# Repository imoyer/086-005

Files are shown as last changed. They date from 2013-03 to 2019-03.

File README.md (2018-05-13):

# 086-005

Gestalt Single Stepper Node Firmware

## Introduction

This is the firware the Single Node board used in the Gestalt project by Ilan and Nadya. Which is nice. In this repository you will find files needed to program your Gestalt Single Stepper Node. You can find the files for PCB production in the [board](board) folder of this repository. Pick your revision (e.g. `rev0.4`) and make your own board!

## Installation

This repository contains [Makefile](Makefile) which is used by `make` to do the following.

1. Burn the firmware
2. Set the fuses

At the moment it is configured to use the **AVRISP mkII**. To make it work with FabISP or other AVR programmer, a lot of people will be happy if you add your custom code and make a pull request.

**First** make sure that your AVR programmer is connected. There are many ways to do it, I used `lsusb` on a MacOS system.

```
lsusb
```

The following is what I got in the list.

```
Atmel Corporation AVRISP mkII
```

Which is exactly what I need to proceed. We assume that things like `avrdude` or [CrossPack](https://www.obdev.at/products/crosspack/index.html) are already installed.

**Second**, make sure your Gestalt Node is properly connected to a power source, FTDI and AVR programmer.

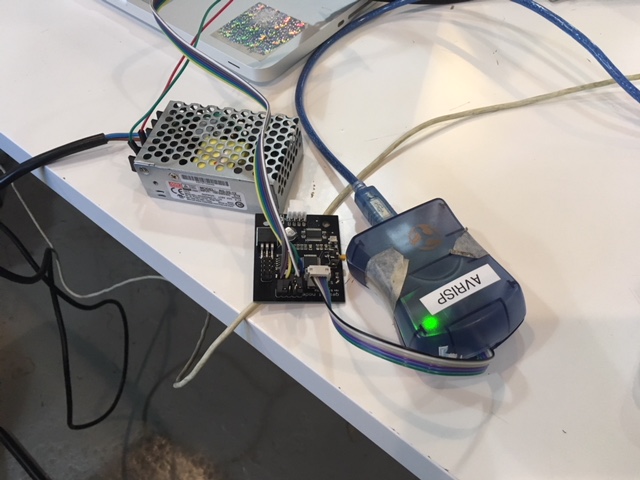
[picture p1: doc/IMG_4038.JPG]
Connected to AVR programmer


At this point you can use `make` to burn the firmware.

```
make program-avrisp2
```

You should see output with things that look like progress bars and a polite **Thank you!** at the end. 

**Third** make sure that you set the fuses. For that you have to use `make` once more.

```
make program-avrisp2-fuses
```

It might ask you to reset a fuse on the way, **just hit ENTER** unless you know what you are doing.

**Congratulations!** Your Gestalt Node is ready to be used. Now go to the [pygestalt](https://github.com/nadya/pygestalt) repository and continue from there.

## Contributing

Please add anything weird to the issue tracker of this repository. If you see how you can improve things directly, submit a pull request.

Thank you!

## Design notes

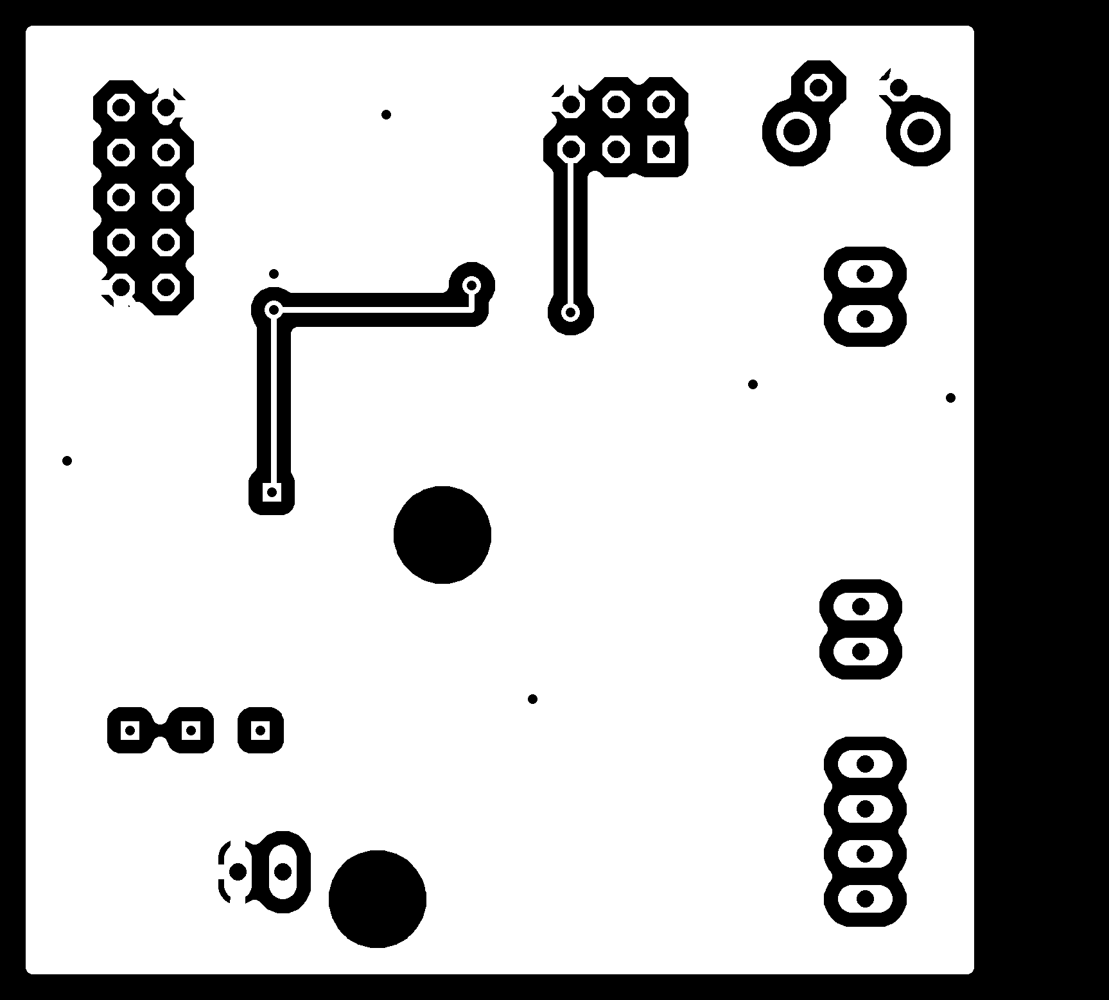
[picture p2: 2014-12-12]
board/extruder/extruder-bottom.png

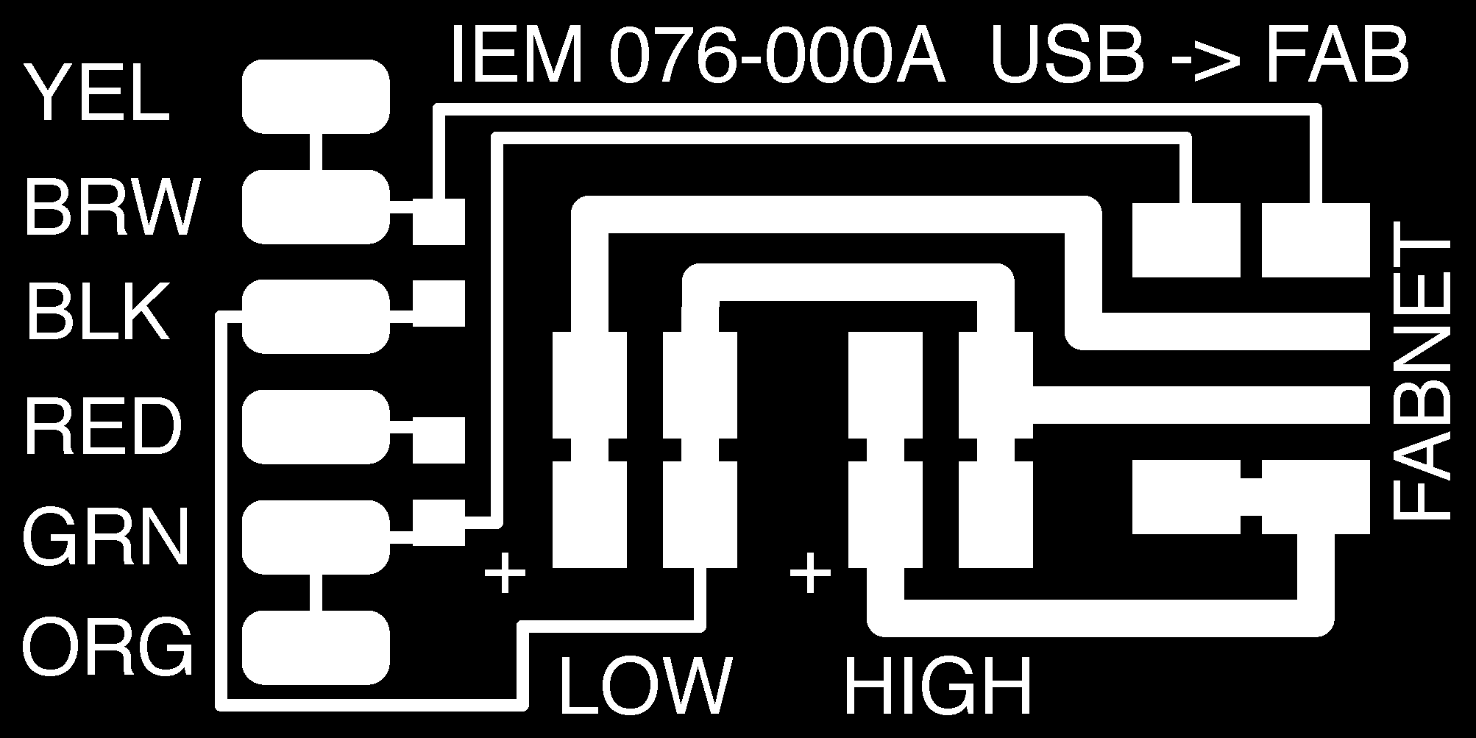
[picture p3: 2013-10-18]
board/fabnet_adapter/076-000Ar1.png

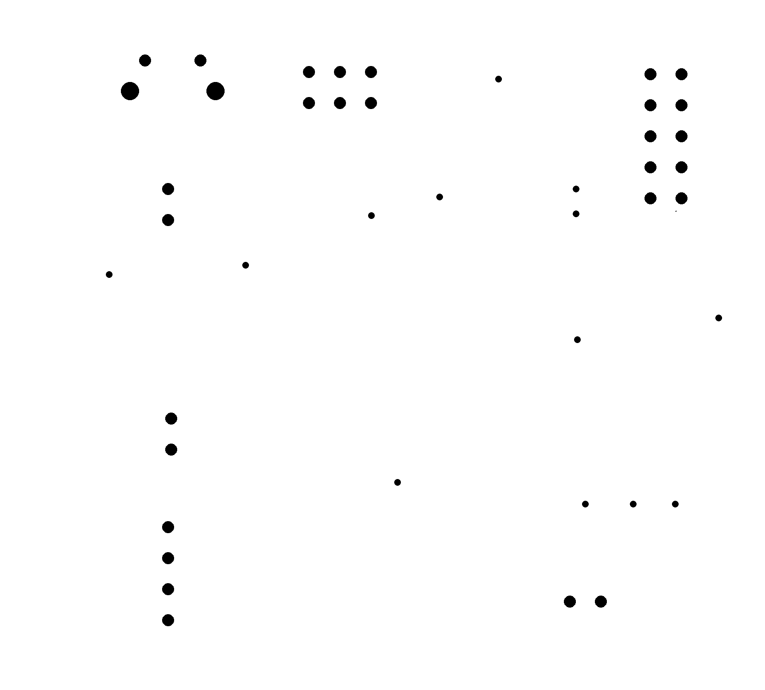
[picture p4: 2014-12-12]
board/extruder/extruder-holes.png

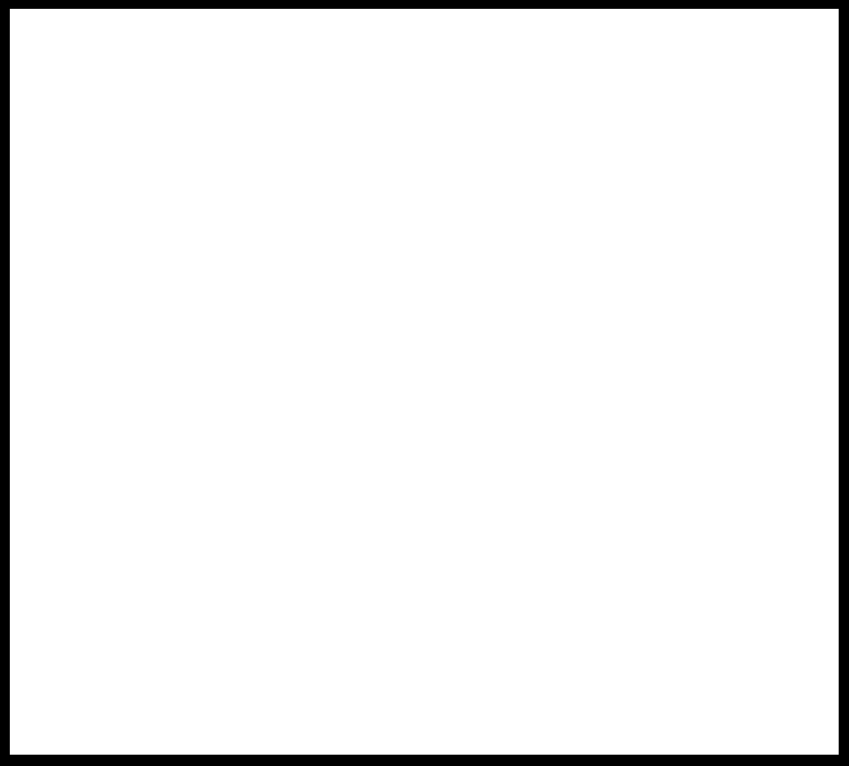
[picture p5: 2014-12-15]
board/extruder/extruder-outline.png

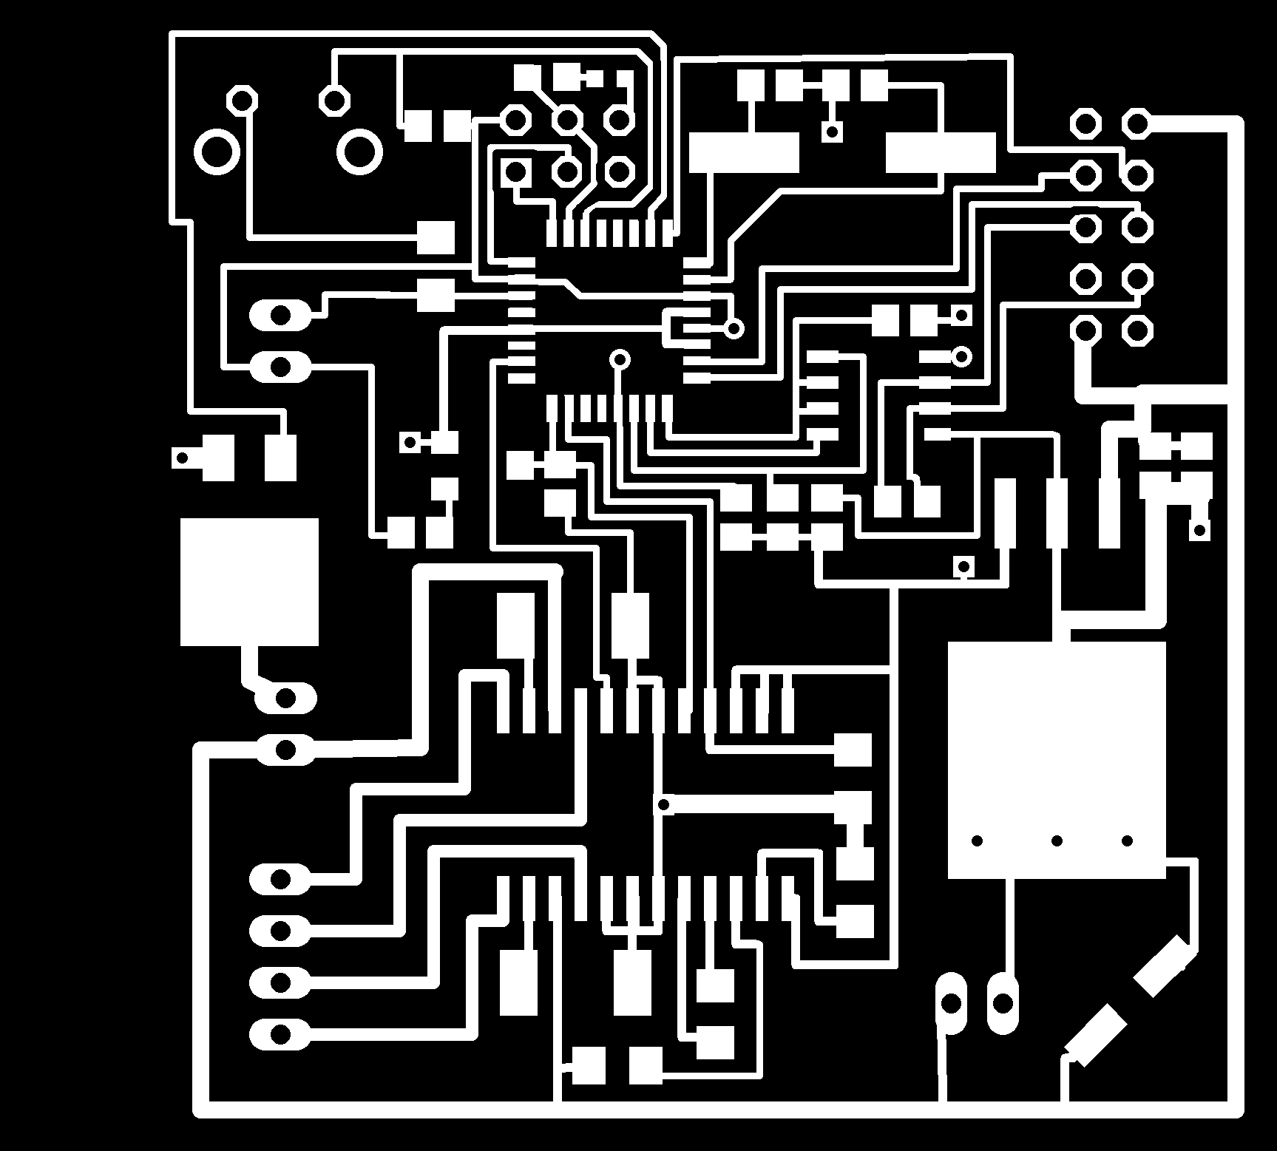
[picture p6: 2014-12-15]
board/extruder/extruder-traces.png

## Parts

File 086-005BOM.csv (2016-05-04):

Name | Description | package | Manufacturer | part | nr | Vendor | part | nr | quantity | unit | price | extended | price
gestalt | network | BOM
usb | to | serial | cable | CABLE | USB | RS485 | WIRE | END | 1.8M |  | USB-RS485-WE-1800-BT | 768-1041-ND | 1 | 30 | 30
fabbus | plugs | 10pin | idc | connector | 0.1 | in
fabbus | ribbon | cabling | 22 | gauge | 10 | wire | ribbon
fabbus | resistors | 540 | ohms?
gestalt | node | BOM
motor | jack | molex | kk | kk | 22-05-3041 | WM4302-ND | 1 | 0.71 | 0.71
motor | plug | molex | kk | with | wings | kk | 22013047 | WM2002-ND | 1 | 0.2 | 0.2 | note | don't | need | this | for | node
motor | crimps | molex | kk | kk | 8500114 | WM1114-ND | 4 | 0.18 | 0.72 | note | don't | need | this | for | node
microcontroller | IC | MCU | 8BIT | 32KB | FLASH | 32TQFP | tqfp | atmega328p | ATMEGA328P-ANRCT-ND | 1 | 4.03 | 4.03
stepper | motor | driver | IC | MOTOR | DRIVER | PAR | 24TSSOP | 24tssop | A4982SLPTR-T | 620-1352-1-ND | 1 | 3.66 | 3.66
differential | bus | transceiver | IC | DIFF | BUS | TRANSCEIVER | 8-SOIC | 8-soic | SN75176AD | 296-6857-5-ND | 1 | 0.96 | 0.96
5v | regulator | IC | REG | LDO | 5V | 1.5A | DDPAK | d2pak-3 | TL780-05CKTTR | 296-20777-1-ND | 1 | 0.95 | 0.95
button | SWITCH | TACTILE | SPST-NO | 0.05A | 24V | Through Hole, Right Angle | B3F-3152 | SW410-ND | 1 | 0.54 | 0.54
potentiometer | TRIMMER | 5K | OHM | 0.25W | SMD | top adjustment, Gull Wing | PVG3G502C01R00 | 490-6996-1-ND | 1 | 1.04 | 1.04
40mm | x | 40mm | fan | FAN | 40X10MM | 12VDC | 0.96W | 7CFM |  | MB40101V2-000U-A99 | 259-1564-ND | 1 | 1 | 4.53 | note, don't need this
fan | connector |  |  |  |  |  |  | 0 | note, don't need this
18.432MHz | crystal | CRYSTAL | 18.432MHZ | 18PF | SMD | hc49/us | ECS-184-18-5PX-TR | XC1285CT-ND | 1 | 0.56 | 0.56
avrisp | header | 6 | pin | idc | connector | 0.1 | inch | 2row3pos | 0.1 | inch | smt | FCI | - | 95278-101A06LF | 609-3487-1-ND | 1 | 1.1 | 1.1
fabbus | header | 10 | pin | idc | connector | 0.1 | inch | 2row5pos | 0.1inch | smt | FCI | - | 95278-101A10LF | 609-3483-6-ND | 1 | 1.27 | 1.27
capacitor | 22 | pF | c0805 |  |  | 2 | 0.1 | 0.2
capacitor | 1 | nF | c0805 |  |  | 1 | 0.1 | 0.1
capacitor | 200 | nF | c0805 |  |  | 2 | 0.1 | 0.2 | note | this | can | be | replaced | with | 0.22uF | if | convenient
capacitor | 0.22uF | c0805 |  |  | 2 | 0.1 | 0.2
capacitor | 0.1 | uF | c0805 |  |  | 3 | 0.1 | 0.3
polarized | capacitor | 100 | uF | panasonic | D | (6.3mm | diameter) | EEE-FTH101XAP | PCE5024CT-ND | 1 | 0.92 | 0.92
current | sense | resistor | 0.1 ohms, 1W | r1206 |  | P.10AVCT-ND | 2 | 0.9 | 1.8 |  |  |  |  | note this is 1W but you can also use down to ¼W
resistor | 10k | ohms | r0805 |  |  | 8 | 0.1 | 0.8
resistor | 120 | ohms | r0805 |  |  | 1 | 0.1 | 0.1
resistor | 560 | ohms | r0805 |  |  | 1 | 0.1 | 0.1
led | blue | led0603 |  |  | 1 | 0.17 | 0.17
 |  |  |  |  |  |  | 24.53

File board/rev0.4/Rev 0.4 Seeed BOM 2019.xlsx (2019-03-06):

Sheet: Seeed BOM Format
Designator | MPN | Qty | Link
C1,C2,C11 | CC0805ZRY5V9BB104 | 3 | https://www.mouser.fi/ProductDetail/Yageo/CC0805ZRY5V9BB104?qs=sGAEpiMZZMs0AnBnWHyRQMMzfhmH8IQXmNpj6dF8FW8%3D
C3,C4 | 08055C224J4Z2A | 2 | https://www.mouser.fi/ProductDetail/AVX/08055C224J4Z2A
C5 | 865080142007 | 1 | https://www.mouser.fi/ProductDetail/Wurth-Electronics/865080142007
C6,C7 | CC0805JRNPO9BN220 | 2 | https://www.mouser.fi/ProductDetail/Yageo/CC0805JRNPO9BN220
C8 | CC0805KRX7R0BB102 | 1 | https://www.mouser.fi/ProductDetail/Yageo/CC0805KRX7R0BB102
C20,C21 | GCM219R71C204JA37J | 2 | https://www.mouser.fi/ProductDetail/Murata-Electronics/GCM219R71C204JA37J
IC1 | ATXMEGA32E5-AU | 1 | https://www.mouser.fi/ProductDetail/Microchip-Technology-Atmel/ATXMEGA32E5-AU
IC3 | A4982SLPTR-T | 1 | https://www.digikey.fi/product-detail/en/allegro-microsystems-llc/A4982SLPTR-T/620-1352-1-ND/2295513
IC6 | SN75176AD | 1 | https://www.digikey.fi/product-detail/en/texas-instruments/SN75176ADR/296-14955-1-ND/562533
IC8 | TL780-05CKTTR | 1 | https://www.digikey.fi/product-detail/en/texas-instruments/TL780-05CKTTRG3/296-50534-1-ND/9685673
J1,J4 | 95278-101A10LF | 2 | https://www.mouser.fi/ProductDetail/Amphenol-FCI/95278-101A10LF
J2 | 95278-101A06LF | 1 | https://www.mouser.fi/ProductDetail/Amphenol-FCI/95278-101A06LF
J3 | 22-05-3041 | 1 | https://www.mouser.fi/ProductDetail/Molex/22-05-3041
LED1 | LSM0603443V | 1 | https://www.digikey.fi/product-detail/en/visual-communications-company-vcc/LSM0603443V/LSM0603443VCT-ND/9486728
Q1 | ECS-184-18-5PX-TR | 1 | https://www.digikey.fi/product-detail/en/ecs-inc/ECS-184-18-5PX-TR/XC1285CT-ND/827749
R1, R2 | ERJ-8BWJR100V | 2 | https://www.digikey.fi/product-detail/en/panasonic-electronic-components/ERJ-8BWJR100V/P.10AVCT-ND/1711731
R3,R4,R5,R6,R7,R9,R11,R31 | RMCF0805FT10K0 | 8 | https://www.digikey.fi/product-detail/en/stackpole-electronics-inc/RMCF0805FT10K0/RMCF0805FT10K0CT-ND/1942435
R8 | CRCW0805560RFKEAC | 1 | https://www.mouser.fi/ProductDetail/Vishay/CRCW0805560RFKEAC
R10 | PVG3G502C01R00 | 1 | https://www.digikey.fi/product-detail/en/bourns-inc/PVG3G502C01R00/490-6996-1-ND/3846193
R32 | RMCF0805JT120R | 1 | https://www.digikey.fi/product-detail/en/stackpole-electronics-inc/RMCF0805JT120R/RMCF0805JT120RCT-ND/1942540
S1 | B3F-3152 | 1 | https://www.digikey.fi/products/en?keywords=B3F-3152

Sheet: Part value requirement
分类 Catalog | 元件值 Part_Value
电感 Inductors | Inductance-Current-Tolerance | 电感值-额定电流-容差
磁珠 Ferrite Bead | Impedance-Current Rating | 阻抗-额定电流
电容 Capacitors | Capacitance-Voltage Rated-Tolerance-Dielectric | 电容值-额定电压-容差-材质
电阻 Resistors | Resistance-Tolerance-Power | 电阻值-功率-容差
无源晶振 Crystals | Frequency-Frequency Tolerance-Load Capacitance-ESR (Equivalent Series Resistance) | 频率-频率公差-负载电容-等效串联电阻
有源晶振 Crystal Oscillator | Frequency-Frequency Tolerance-Load Capacitance-ESR (Equivalent Series Resistance) | 频率-频率公差-负载电容-等效串联电阻

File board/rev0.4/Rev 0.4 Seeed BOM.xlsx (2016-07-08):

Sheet: Seeed BOM Format
Electronic Engineering BOM List
Product Name： Gestalt Node
Version：0.3
Issue Date：June, 2014
Item No. (序号) | Reference Des (上件位置) | Qty (用量) | Catalog (分类） | Part_Description (规格描述) | Part_Value （元件值） | Part_Package （元件封装） | Manufacturers Name (使用厂牌名称) | Manufacturers Part No. (使用厂牌型号) | Distributors Name （供应商名称） | Distributors Part No. (供貨商型号) | Unit Price （单价） | Price Break To Use （价格分段的购买量） | Notes/Remark （备注）
Example（填写范例）
1 | C1, C2, C11 | 3 | Capacitor | CAP CER 0.1UF 50V Y5V 0805 | 0.1uF | C0805
2 | C3, C4 | 2 | Capacitor | CAP CER 0.22UF 50V X7R 0805 | 0.22uF | C0805
3 | C5 | 1 | Capacitor | CAP ALUM 100UF 20% 6.3V SMD | 100uF | PANASONIC_D | Panasonic Electronic Components | EEE-0JA101SP | Digikey | PCE3852CT-ND
4 | C6, C7 | 2 | Capacitor | CAP CER 22PF 50V NP0 0805 | 22pF | C0805
5 | C8 | 1 | Capacitor | CAP CER SMD 0805 1nF 100V | 1nF | C0805
6 | C20, C21 | 2 | Capacitor | CAP CER 200nF 0805 | 200nF | C0805
7 | IC1 | 1 | IC | IC MCU 8BIT 32KB FLASH 32TQFP | MEGA48/88/168-AU | TQFP32-08 | Atmel | ATMEGA328P-ANR | Digikey | ATMEGA328P-ANRCT-ND
8 | IC3 | 1 | IC | IC MOTOR DRIVER PAR 24TSSOP | A4982 | TSSOP24_LP | Allegro MicroSystems, LLC | A4982SLPTR-T | Digikey | 620-1352-1-ND
9 | IC6 | 1 | IC | IC DIFF BUS TRANSCEIVER 8-SOIC | 75176AD | D_R-PDSO-G8 | Texas Instruments | SN75176AD | Digikey | 296-6857-5-ND
10 | IC8 | 1 | IC | IC REG LDO 5V 1.5A DDPAK | TL780_VREG | D2PAK-3 | Texas Instruments | TL780-05CKTTR | Digikey | 296-20777-1-ND
11 | J1, J4 | 2 | OTHER | 10 pin idc connector .1 inch |  | 2X05 | FCI | FCI - 95278-101A10LF | Digikey | 609-3483-6-ND
12 | J2 | 1 | OTHER | 6 pin idc connector .1 inch | AVR-ISP-6VERT | AVR-ISP-6 | FCI | FCI - 95278-101A06LF | Digikey | 609-3487-1-ND
13 | J3 | 1 | OTHER | CONN HEADER 4POS .100 R/A TIN | KK-4P | 2007100 | Molex, LLC | 22053041 | Digikey | WM4302-ND
14 | LED1 | 1 | Diode | LED BLUE CLEAR 0603 SMD |  | CHIPLED_0603
15 | Q1 | 1 | OTHER | CRYSTAL 18.432MHZ 18PF SMD | 18.432MHz | HC49UP | ECS Inc | ECS-184-18-5PX-TR | Digikey | XC1285CT-ND
16 | R1, R2 | 2 | Resister | RES SMD 0.1 OHM 5% 1W 1206 | 0.1 | R1206
17 | R3, R4, R5, R6, R7, R9, R11, R31 | 8 | Resister | RES SMD 10K OHM 1% 1/8W 0805 | 10k | R0805
18 | R8 | 1 | Resister | RES SMD 560 OHM 5% 1/8W 0805 | 560 | R0805
19 | R10 | 1 | Resister | TRIMMER 5K OHM 0.25W SMD | 5K | BOURN_TRIM | Murata Electronics North America | PVG3G502C01R00 | Digikey | 490-6996-1-ND
20 | R32 | 1 | Resister | RES SMD 120 OHM 5% 1/8W 0805 | 120 | R0805
21 | S1 | 1 | OTHER | SWITCH TACTILE SPST-NO 0.05A 24V |  | B3F-31XX | Omron Electronics Inc-EMC Div | B3F-3152 | Digikey | SW410-ND
1. Recommended Distributor: Digi-Key, Mouser, Avnet Express, Farnell.
2. Catalog: Capacitor,Resister,Diode,Connector,Transistor,IC,PROTECTOR CATEGORY,OTHER
3. Required Fields: Item No, Reference Des, Qty, Catalog, Part_Value, Part Package
Optional Fields: Part_Description, Manufacturers Name, Manufacturers Part No, Distributors Name, Distributors Part No, Unit Cost, Price break to use, Notes/Remark

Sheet: Part value requirement
分类 Catalog | 元件值 Part_Value
电感 Inductors | Inductance-Current-Tolerance | 电感值-额定电流-容差
磁珠 Ferrite Bead | Impedance-Current Rating | 阻抗-额定电流
电容 Capacitors | Capacitance-Voltage Rated-Tolerance-Dielectric | 电容值-额定电压-容差-材质
电阻 Resistors | Resistance-Tolerance-Power | 电阻值-功率-容差
无源晶振 Crystals | Frequency-Frequency Tolerance-Load Capacitance-ESR (Equivalent Series Resistance) | 频率-频率公差-负载电容-等效串联电阻
有源晶振 Crystal Oscillator | Frequency-Frequency Tolerance-Load Capacitance-ESR (Equivalent Series Resistance) | 频率-频率公差-负载电容-等效串联电阻

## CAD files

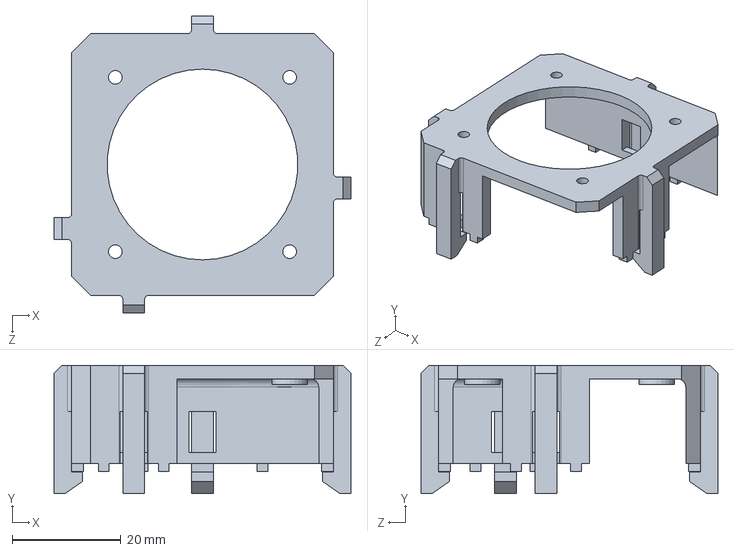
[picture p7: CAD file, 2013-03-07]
MCAD/086-005_MotorMount_Fan.SLDPRT
54.5 x 23.6 x 54.5 mm

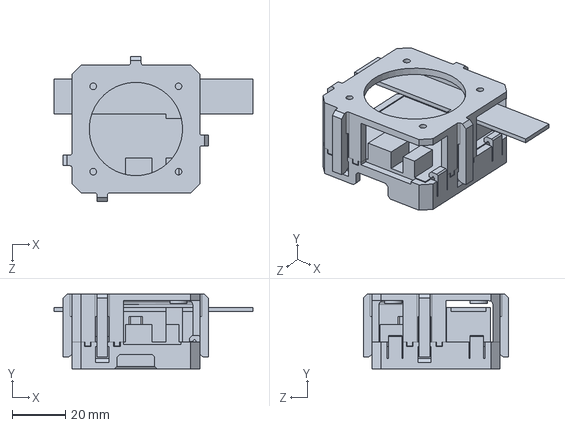
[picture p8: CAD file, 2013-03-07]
MCAD/086-005_MotorMount_Master.SLDPRT
74.6 x 28.1 x 54.5 mm

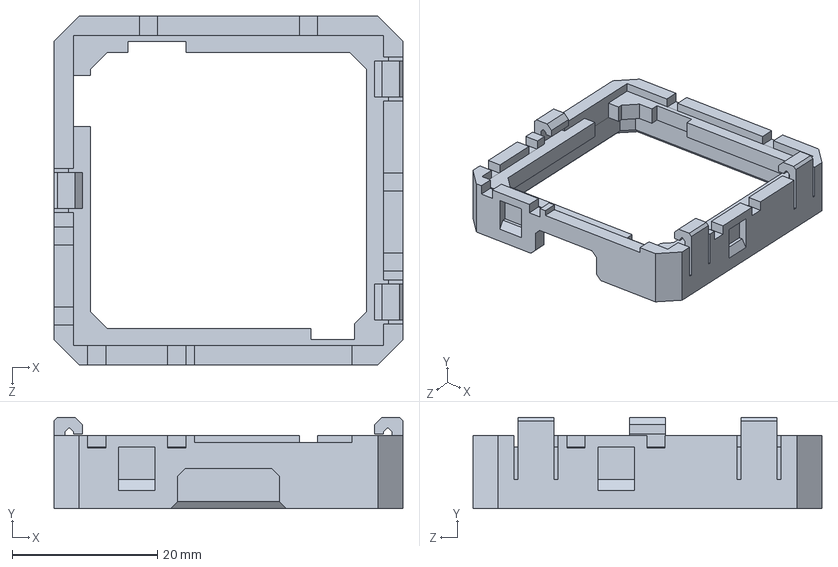
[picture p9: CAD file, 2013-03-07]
MCAD/086-005_MotorMount_Mount.SLDPRT
48.0 x 12.6 x 48.0 mm

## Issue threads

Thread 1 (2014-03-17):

USB RS485 cable died

nadya, 2014-03-17:
Not sure if this is a reproducible issue but I'm going to try-- basically my rs485 cable got fried and I'm not sure why except that maybe it shares power w the spindle motor and needs to be protected more. We should maybe add protection to the fabnet board for messy power.

Closed 2019-03-01.

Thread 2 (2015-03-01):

Boards available?

tiefpunkt, 2015-03-01:
Not really an issue, more a question: Are there any boards available for sale? Would love to try this out, but don't have any possibility to make PCBs myself right now.

Cheers,
Severin

imoyer, 2015-03-02:
Hi Severin,

Thanks for getting in touch. Unfortunately these aren’t available for sale now. I just used Seeedstudio for the first time and it was super cheap and very fast, so maybe that could be a good option for you. Although you’d need to assemble them yourself.

Best,
Ilan

On Mar 1, 2015, at 4:27 AM, Severin Schols <notifications@github.com<mailto:notifications@github.com>> wrote:

Not really an issue, more a question: Are there any boards available for sale? Would love to try this out, but don't have any possibility to make PCBs myself right now.

Cheers,
Severin

—
Reply to this email directly or view it on GitHub<https://github.com/imoyer/086-005/issues/2>.

neosoyo, 2016-12-02:
hi guys, i've tried to open the sch on eagle-cad and seems to be corrupted..
I receive this message from eagle-cad:

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

tried on 6.4 version and 7.7 version, ubuntu and windows, same error..

I want to contribute with a kicad version of the board and a single sided version too, without smd components, in Brazil it's quite annoying to find smd... so if someone could provide me with a schematic pdf, i really appreciate it!

Thanks

kr15h, 2019-02-27:
@imoyer are there any special settings that you used on Seeed Studio? Maybe you can share the ones you used. I want to order 20pcs of rev0.4.

nadya, 2019-03-01:
@kr15h the seeed BOM is in the rev0.4 folder, and the board settings are FR4, 2-layer, 1.6mm PCB, 1oz copper, pads finished with hasl-lead free, with solder mask cover.

This is what I told them about how to flash and test: "For the testing, this is what I do:

For the atmega328p, can you burn the fuses to
	avrdude -c avrisp2 -P usb -p m328p -U efuse:w:0x5:m -F
	avrdude -c avrisp2 -P usb -p m328p -U hfuse:w:0xD8:m -F
	avrdude -c avrisp2 -P usb -p m328p -U lfuse:w:0xEF:m -F

And load the hex file 086-005a.hex.

To test the board, I plug in a stepper motor and I run a program and
communicate with the board over a RS-485 cable. I splice the cable with
a power cable.

For the software, you'd need to install this library:
http://github.com/nadya/pygestalt
and in the examples folder, run the python script htmaa/single_node.py

The software will prompt you to press the push button, and will move the
motor.
"

kr15h, 2019-03-03:
Thanks @nadya !!!

kr15h, 2019-03-03:
Seems like now SeeedStudio requires a different structure of the BOM. Only 4 columns. I am working on it and will submit a pull request.

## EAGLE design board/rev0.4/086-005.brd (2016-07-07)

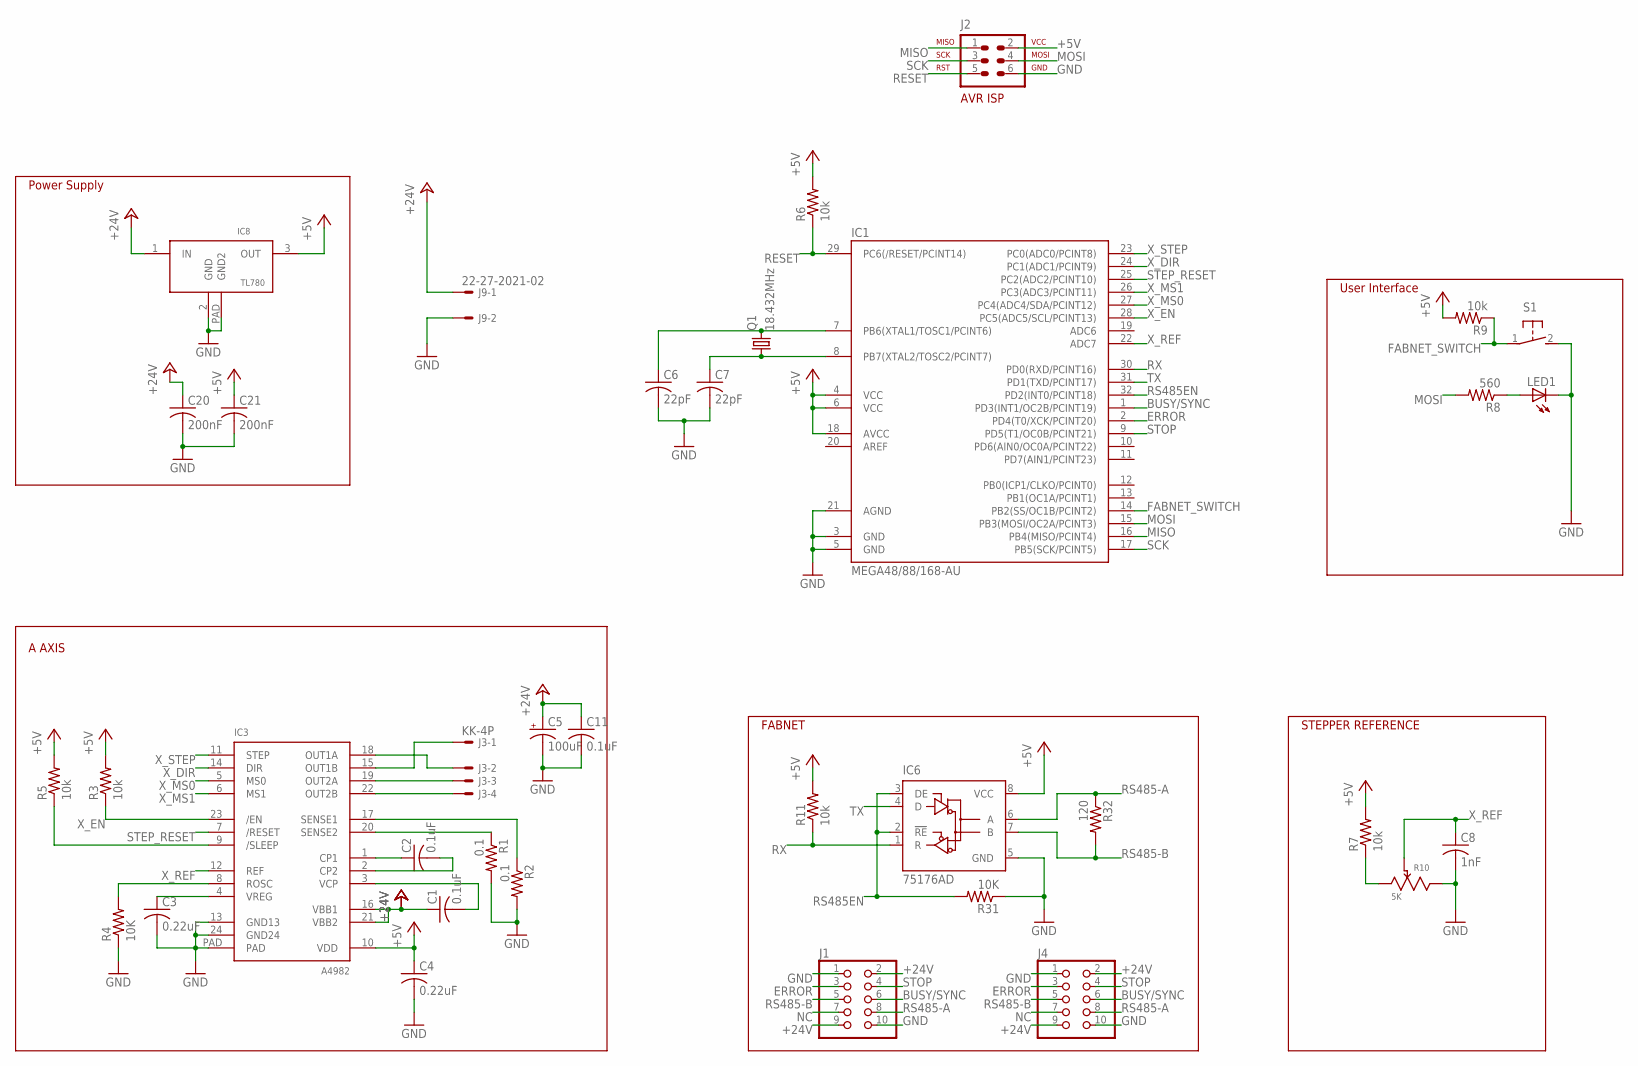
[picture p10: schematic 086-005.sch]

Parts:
C1, C2, C11: 0.1uF; C0805
C3, C4: 0.22uF; C0805
C5: 100uF; PANASONIC_D
C6, C7: 22pF; C0805
C8: 1nF; C0805
C20, C21: 200nF; C0805
IC1: MEGA48/88/168-AU; TQFP32-08
IC3: A4982; TSSOP24_LP
IC6: 75176AD; D_R-PDSO-G8
IC8: TL780_VREG; D2PAK-3
J1, J4: PINHD-2X5; 2X05
J2: AVR-ISP-6VERT; AVR-ISP-6
J3: KK-4P; 7395-04
J9: 22-27-2021-02; 6410-02
LED1: LEDCHIPLED_0603; CHIPLED_0603
Q1: 18.432MHz; HC49UP
R1, R2: 0.1; R1206
R3, R5, R6, R7, R9, R11: 10k; R0805
R4, R31: 10K; R0805
R8: 560; R0805
R10: 5K; BOURN_TRIM
R32: 120; R0805
S1: 31-XX; B3F-31XX

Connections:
+5V: C4.1, C21.1, IC1.4 (VCC), IC1.6 (VCC), IC1.18 (AVCC), IC3.10 (VDD), IC6.8 (VCC), IC8.3 (OUT), J2.2, R3.2, R5.2, R6.2, R7.2, R9.2, R11.2
+24V: C1.1, C5.+, C11.1, C20.1, IC3.16 (VBB1), IC3.21 (VBB2), IC8.1 (IN), J1.2, J1.9, J4.2, J4.9, J9.1
BUSY/SYNC: IC1.1 (PD3(INT1/OC2B/PCINT19)), J1.6, J4.6
ERROR: IC1.2 (PD4(T0/XCK/PCINT20)), J1.3, J4.3
FABNET_SWITCH: IC1.14 (PB2(SS/OC1B/PCINT2)), R9.1, S1.1
GND: C3.2, C4.2, C5.-, C6.2, C7.2, C8.2, C11.2, C20.2, C21.2, IC1.3 (GND), IC1.5 (GND), IC1.21 (AGND), IC3.13 (GND13), IC3.24 (GND24), IC3.PAD, IC6.5 (GND), IC8.2 (GND), IC8.PAD (GND2), J1.1, J1.10, J2.6, J4.1, J4.10, J9.2, LED1.C, R1.2, R2.2, R4.1, R10.3, R31.1, S1.2 (S)
MISO: IC1.16 (PB4(MISO/PCINT4)), J2.1
MOSI: IC1.15 (PB3(MOSI/OC2A/PCINT3)), J2.4, R8.2
N2354: R7.1, R10.1
unnamed: C6.1, IC1.7 (PB6(XTAL1/TOSC1/PCINT6)), Q1.2
unnamed: C7.1, IC1.8 (PB7(XTAL2/TOSC2/PCINT7)), Q1.1
unnamed: IC3.19 (OUT2A), J3.3
unnamed: IC3.22 (OUT2B), J3.4
unnamed: LED1.A, R8.1
unnamed: IC3.18 (OUT1A), J3.2
unnamed: IC3.15 (OUT1B), J3.1
unnamed: IC3.20 (SENSE2), R1.1
unnamed: IC3.17 (SENSE1), R2.1
unnamed: IC3.8 (ROSC), R4.2
unnamed: C1.2, IC3.3 (VCP)
unnamed: C2.1, IC3.1 (CP1)
unnamed: C2.2, IC3.2 (CP2)
unnamed: IC3.9 (/SLEEP), R5.1
unnamed: C3.1, IC3.4 (VREG)
NC: J1.7, J4.7
RESET: IC1.29 (PC6(/RESET/PCINT14)), J2.5, R6.1
RS485-A: IC6.6 (A), J1.8, J4.8, R32.1
RS485-B: IC6.7 (B), J1.5, J4.5, R32.2
RS485EN: IC1.32 (PD2(INT0/PCINT18)), IC6.2 (!RE), IC6.3 (DE), R31.2
RX: IC1.30 (PD0(RXD/PCINT16)), IC6.1 (R), R11.1
SCK: IC1.17 (PB5(SCK/PCINT5)), J2.3
STEP_RESET: IC1.25 (PC2(ADC2/PCINT10)), IC3.7 (/RESET)
STOP: IC1.9 (PD5(T1/OC0B/PCINT21)), J1.4, J4.4
TX: IC1.31 (PD1(TXD/PCINT17)), IC6.4 (D)
X_DIR: IC1.24 (PC1(ADC1/PCINT9)), IC3.14 (DIR)
X_EN: IC1.28 (PC5(ADC5/SCL/PCINT13)), IC3.23 (/EN), R3.1
X_MS0: IC1.27 (PC4(ADC4/SDA/PCINT12)), IC3.5 (MS0)
X_MS1: IC1.26 (PC3(ADC3/PCINT11)), IC3.6 (MS1)
X_REF: C8.1, IC1.22 (ADC7), IC3.12 (REF), R10.2
X_STEP: IC1.23 (PC0(ADC0/PCINT8)), IC3.11 (STEP)

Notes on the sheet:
A AXIS
Power Supply
FABNET
STEPPER REFERENCE
User Interface

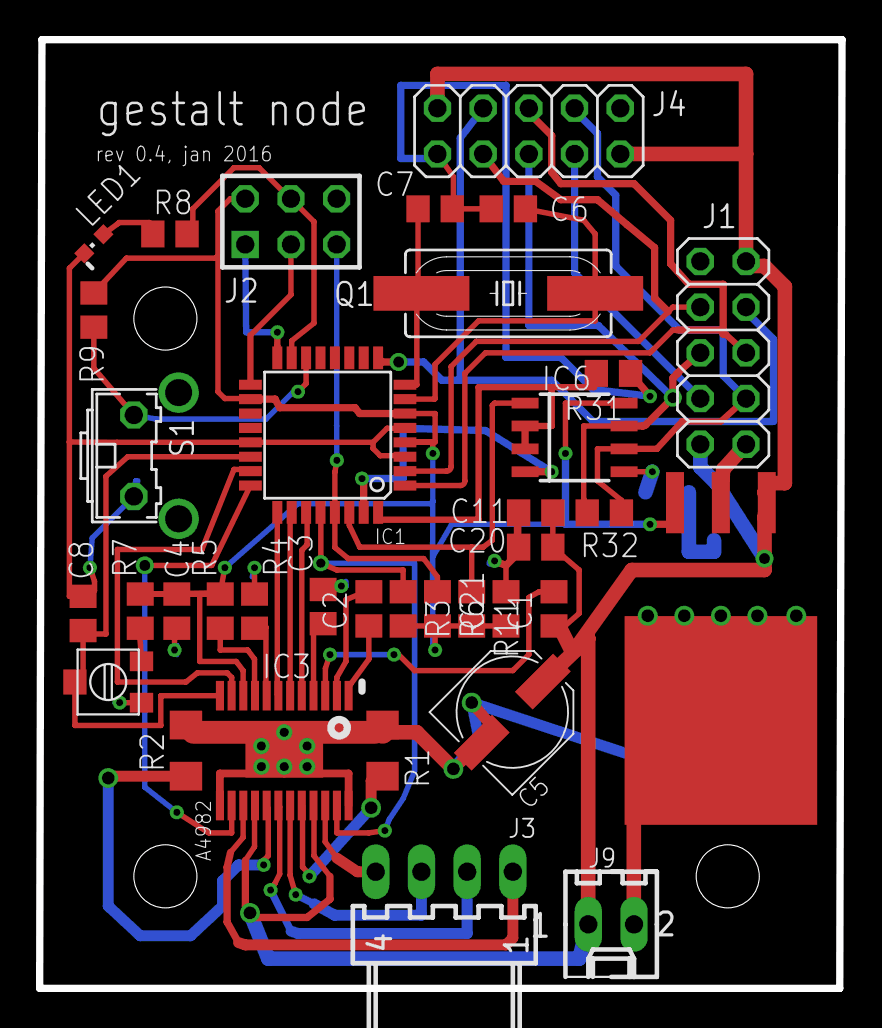
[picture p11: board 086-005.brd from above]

Board: 2 copper layers, 44.6 x 52.7 mm, 36 parts (0 on the bottom side), 40 nets.

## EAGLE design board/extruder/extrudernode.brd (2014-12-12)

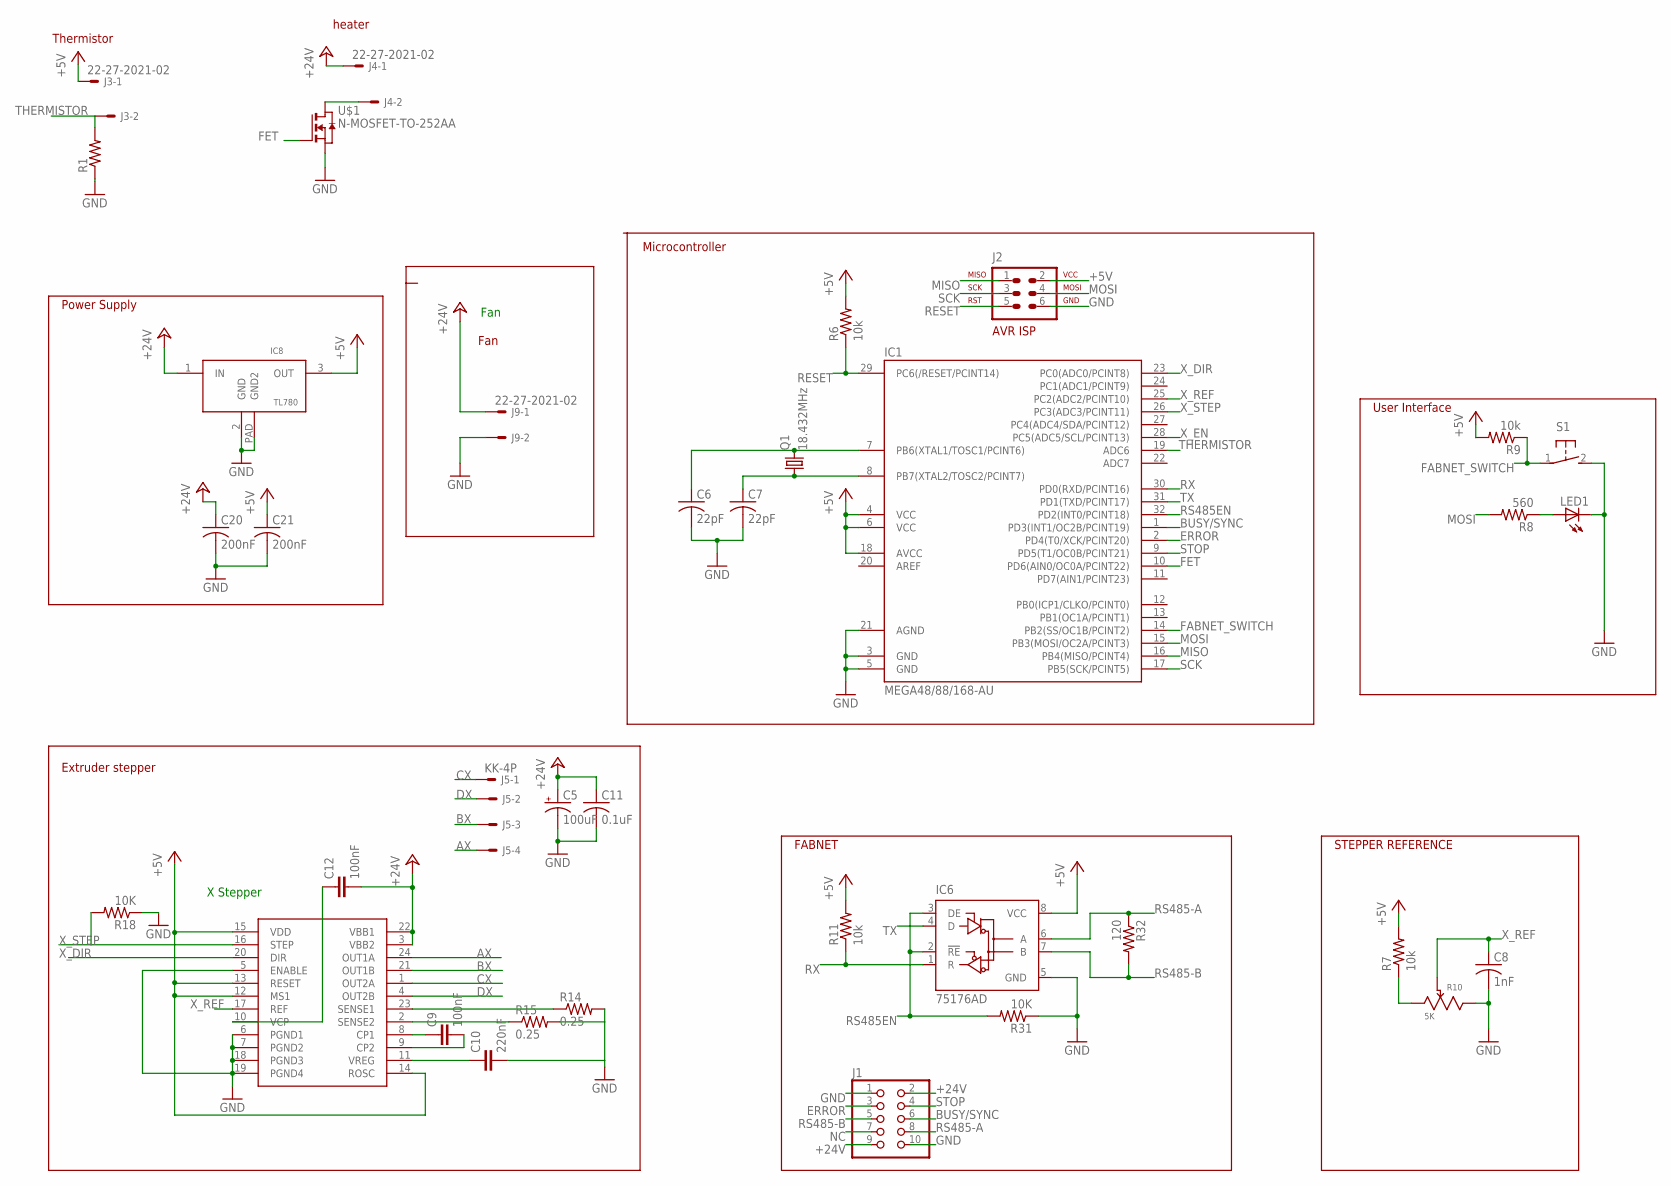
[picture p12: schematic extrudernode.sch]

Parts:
C5: 100uF; PANASONIC_D
C6, C7: 22pF; C0805@1
C8: 1nF; C0805@1
C9, C12: 100nF; C1206
C10: 220nF; C1206
C11: 0.1uF; C0805@1
C20, C21: 200nF; C0805@1
DRIVER3: A3982; SO24W
IC1: MEGA48/88/168-AU; TQFP32-08
IC6: 75176AD; D_R-PDSO-G8
IC8: TL780_VREG; D2PAK-3
J1: PINHD-2X5; 2X05
J2: AVR-ISP-6VERT; AVR-ISP-6
J3, J4, J9: 22-27-2021-02; 6410-02
J5: KK-4P; 7395-04
LED1: LEDCHIPLED_0603; CHIPLED_0603
Q1: 18.432MHz; HC49UP
R1: RESISTOR1206; 1206
R6, R7, R9, R11: 10k; R0805
R8: 560; R0805
R10: 5K; BOURN_TRIM
R14, R15: 0.25; R2512
R18: 10K; R1206
R31: 10K; R0805
R32: 120; R0805
S1: 31-XX; B3F-31XX
U$1: N-MOSFET-TO-252AA; TO-252AA

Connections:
+5V: C21.1, DRIVER3.12 (MS1), DRIVER3.13 (RESET), DRIVER3.14 (ROSC), DRIVER3.15 (VDD), IC1.4 (VCC), IC1.6 (VCC), IC1.18 (AVCC), IC6.8 (VCC), IC8.3 (OUT), J2.2, J3.1, R6.2, R7.2, R9.2, R11.2
+24V: C5.+, C11.1, C12.2, C20.1, DRIVER3.3 (VBB2), DRIVER3.22 (VBB1), IC8.1 (IN), J1.2, J1.9, J4.1, J9.1
AX: DRIVER3.24 (OUT1A), J5.4
BUSY/SYNC: IC1.1 (PD3(INT1/OC2B/PCINT19)), J1.6
BX: DRIVER3.21 (OUT1B), J5.3
CX: DRIVER3.1 (OUT2A), J5.1
DX: DRIVER3.4 (OUT2B), J5.2
ERROR: IC1.2 (PD4(T0/XCK/PCINT20)), J1.3
FABNET_SWITCH: IC1.14 (PB2(SS/OC1B/PCINT2)), R9.1, S1.1
FET: IC1.10 (PD6(AIN0/OC0A/PCINT22)), U$1.GATE (G)
GND: C5.-, C6.2, C7.2, C8.2, C10.2, C11.2, C20.2, C21.2, DRIVER3.5 (ENABLE), DRIVER3.6 (PGND1), DRIVER3.7 (PGND2), DRIVER3.18 (PGND3), DRIVER3.19 (PGND4), IC1.3 (GND), IC1.5 (GND), IC1.21 (AGND), IC6.5 (GND), IC8.2 (GND), IC8.PAD (GND2), J1.1, J1.10, J2.6, J9.2, LED1.C, R1.1, R10.3, R14.2, R15.2, R18.1, R31.1, S1.2 (S), U$1.SOURCE (S)
MISO: IC1.16 (PB4(MISO/PCINT4)), J2.1
MOSI: IC1.15 (PB3(MOSI/OC2A/PCINT3)), J2.4, R8.2
N2354: R7.1, R10.1
unnamed: C6.1, IC1.7 (PB6(XTAL1/TOSC1/PCINT6)), Q1.2
unnamed: C7.1, IC1.8 (PB7(XTAL2/TOSC2/PCINT7)), Q1.1
unnamed: LED1.A, R8.1
unnamed: J4.2, U$1.DRAIN (D)
unnamed: DRIVER3.23 (SENSE1), R14.1
unnamed: DRIVER3.2 (SENSE2), R15.1
unnamed: C9.1, DRIVER3.8 (CP1)
unnamed: C9.2, DRIVER3.9 (CP2)
unnamed: C10.1, DRIVER3.11 (VREG)
unnamed: C12.1, DRIVER3.10 (VCP)
NC: J1.7
RESET: IC1.29 (PC6(/RESET/PCINT14)), J2.5, R6.1
RS485-A: IC6.6 (A), J1.8, R32.1
RS485-B: IC6.7 (B), J1.5, R32.2
RS485EN: IC1.32 (PD2(INT0/PCINT18)), IC6.2 (!RE), IC6.3 (DE), R31.2
RX: IC1.30 (PD0(RXD/PCINT16)), IC6.1 (R), R11.1
SCK: IC1.17 (PB5(SCK/PCINT5)), J2.3
STOP: IC1.9 (PD5(T1/OC0B/PCINT21)), J1.4
THERMISTOR: IC1.19 (ADC6), J3.2, R1.2
TX: IC1.31 (PD1(TXD/PCINT17)), IC6.4 (D)
X_DIR: DRIVER3.20 (DIR), IC1.23 (PC0(ADC0/PCINT8))
X_EN: IC1.28 (PC5(ADC5/SCL/PCINT13))
X_REF: C8.1, DRIVER3.17 (REF), IC1.25 (PC2(ADC2/PCINT10)), R10.2
X_STEP: DRIVER3.16 (STEP), IC1.26 (PC3(ADC3/PCINT11)), R18.2

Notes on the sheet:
Extruder stepper
Power Supply
FABNET
STEPPER REFERENCE
User Interface
X Stepper
Fan
Thermistor
heater
Microcontroller

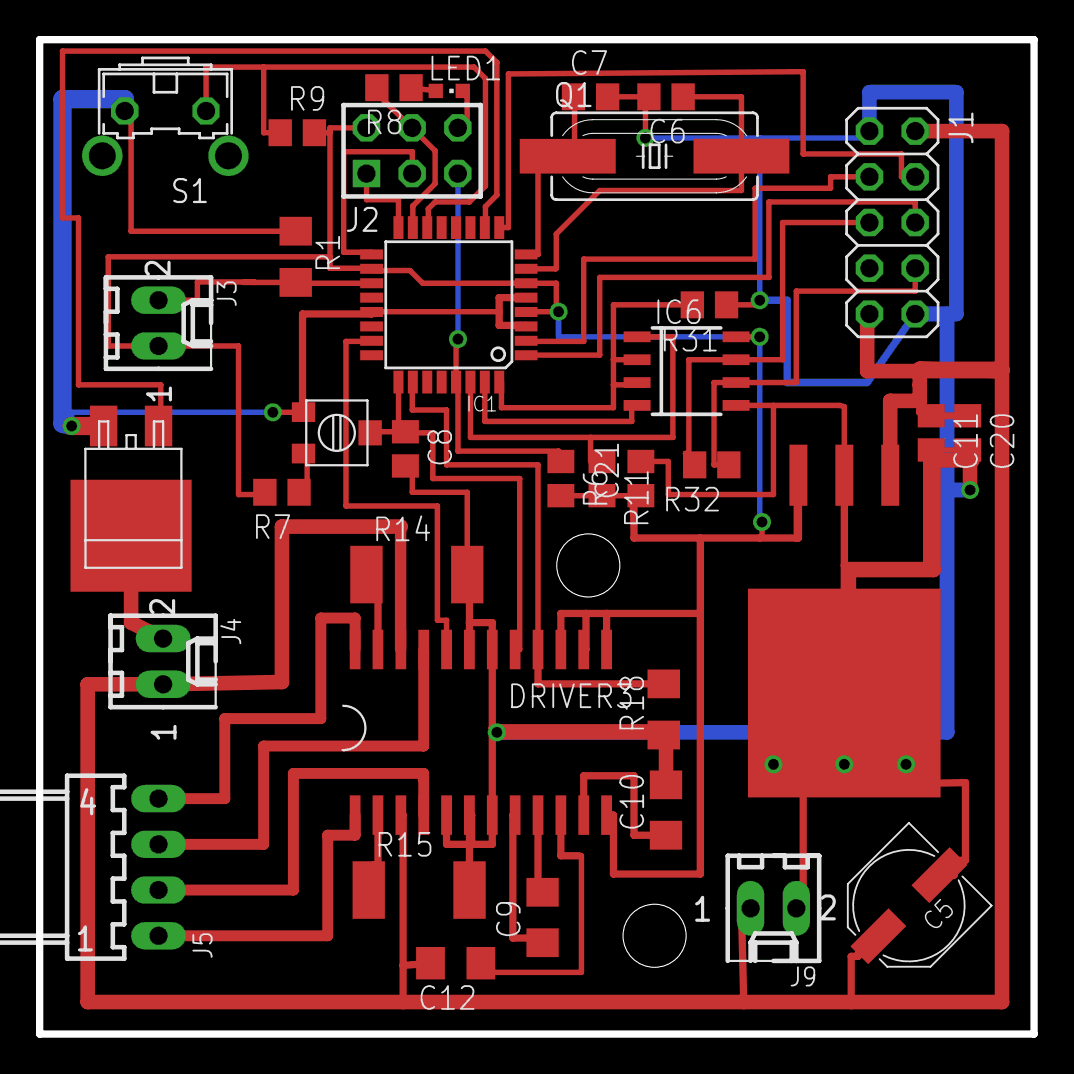
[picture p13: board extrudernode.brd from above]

Board: 2 copper layers, 55.2 x 55.2 mm, 36 parts (0 on the bottom side), 36 nets.

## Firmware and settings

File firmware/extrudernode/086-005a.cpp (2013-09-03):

#include <gestalt.h>
#include <avr/io.h>
#include <avr/delay.h>
#include <avr/interrupt.h>

//STEPPER CONTROL PORT/PIN ASSIGNEMNTS
#define motorPORT   PORTC
#define motorDDR    DDRC
#define motorPIN    PINC
#define motorStep   PC0
#define motorDir    PC1
#define motorReset  PC2
#define motorMS1    PC3
#define motorMS0    PC4
#define motorEnable PC5
//Motor Current REF is on ADC7


//DEFINE NETWORK PORTS
const uint8_t getVrefPort         = 20; //reports back the current motor reference voltage
const uint8_t enableDriverPort    = 21; //enables the drivers
const uint8_t disableDriverPort   = 22; //disables the drivers
const uint8_t movePort            = 23; //move
const uint8_t setVelocityPort     = 24; //sets current velocity
const uint8_t spinStatusPort      = 26; //get spin status

const uint8_t syncPort            = 30; //triggers a sync. This is a soft proxy for the sync control line.

//Move Packet Definition
#define moveMajorSteps  0
#define moveDirections  1
#define moveSteps       2
#define moveAccel       3
#define moveAccelSteps  4
#define moveDeccelSteps 5
#define moveSync        6

//--Move Status Definition
#define statusCode            0
#define statusCurrentKey      1
#define statusStepsRemaining  2
#define statusReadPosition    3
#define statusWritePosition   4

#define velocity0       0
#define velocity1       1


//CONFIGURE URL
char myurl[] = "http://www.fabunit.com/vn/086-005a.py";

//STEP CONTROL VARIABLE AND MEMORY

struct moveSegment{ //8 bytes total
  volatile uint8_t segmentKey; //keeps track of segment number for status reports, pausing, etc.
  volatile uint8_t majorSteps;  //virtual major steps to take
  volatile uint8_t directions; //0b0000000a
  volatile uint8_t steps; //number of steps to take
  volatile uint8_t accel; //accel/decel rate for this segment
  volatile uint8_t accelSteps;  //number of steps over which to accelerate
  volatile uint8_t decelSteps; //number of steps over which to decelerate
  volatile uint8_t waitForSync;  //if>0 then this move is waiting for a synchronization packet.
};

const uint8_t bufferLength = 64;  //512 bytes, on an atmega32x total memory is 2K.
struct moveSegment moveBuffer[bufferLength];  //stores all buffered moves

//CIRCULAR BUFFER INDEXES
//When a new packet comes in, the write buffer position gets incremented and then that location is written to.
//The main process (or maybe the step generator process) detects that the write buffer is ahead of
//the read buffer, and increments the read buffer position and then reads that location into the step generator.
volatile uint8_t readPosition = 0; //gets incremented and then read, so reflects location that was last read
volatile uint8_t writePosition = 0; //gets incremented and then written, so reflects location that was last written to.
volatile uint8_t segmentKeyCounter = 255; //used to pull new segment keys. The counter is incremented, and then a key is pulled.
volatile uint8_t syncSearchPosition = 0; //the last buffer location where a search for a sync packet has been conducted.


//DIRECTION MASKS
const uint8_t aDirectionMask = 1; //only one axis.

//BRESENHAM VARIABLES
//Default units for packets are 1/4 steps, but system is operating at 1/16 steps.
volatile uint16_t majorSteps;
volatile uint16_t majorError; //majorError = majorSteps/2
volatile uint16_t majorStepsRemaining;
volatile int16_t aSteps;
volatile int16_t aError;

//STEP GENERATOR VARIABLES
volatile uint8_t microstepping = 2; //microstep resolution is 4*2^microstepping (base is 1/4 step, this variable is the bit shift)
volatile uint16_t accelSteps = 0; //current segment accel steps
volatile uint16_t decelSteps = 0; //current segment Decel steps
volatile uint8_t uAccel = 0; //current segment acceleration
volatile uint32_t uVelocity = 0;
volatile uint32_t uPosition = 0;  //uSteps
const uint32_t uSteps = 1048576;  //uSteps per step (2^20)
volatile uint8_t waitingForSync = 0;  //this will get set to 1 when the move interrupt is waiting on a sync.
volatile uint8_t antiLockout = 0; //if 1, indicates that velocity should be returned to zero at end of move.


//USER SETUP
void userSetup(){
  setURL(&myurl[0], sizeof(myurl));

  //PIN AND PORT CONFIGURATION FOR SINGLE STEPPER
  //LED
  IO_ledPORT = &PORTB;
  IO_ledDDR = &DDRB;
  IO_ledPIN = &PINB;
  IO_ledPin = 1<<3;

  //FABNET BUTTON
  IO_buttonPORT = &PORTB;
  IO_buttonDDR = &DDRB;
  IO_buttonPIN = &PINB;
  IO_buttonPin = 1<<2;

  //FABNET TXRX
  IO_txrxPORT = &PORTD;
  IO_txrxDDR = &DDRD;
  IO_rxPin = 1<<0;
  IO_txPin = 1<<1;

  //FABNET TX ENABLE
  IO_txEnablePORT = &PORTD;
  IO_txEnableDDR = &DDRD;
  IO_txEnablePin = 1<<2;

  ADMUX = (0<<REFS1)|(1<<REFS0)|(0<<ADLAR)|(0<<MUX3)|(1<<MUX2)|(1<<MUX1)|(1<<MUX0);   //External Reference, Right Adjusted, External Reference
  ADCSRA = (1<<ADEN)|(0<<ADSC)|(0<<ADATE)|(0<<ADIF)|(0<<ADIE)|(1<<ADPS2)|(1<<ADPS1)|(1<<ADPS0);  //Enable ADC, clock source is CLK/128

  motorDDR |= (1<<motorStep)|(1<<motorDir)|(1<<motorReset)|(1<<motorMS1)|(1<<motorMS0)|(1<<motorEnable);  //set all motor pins to outputs
  motorPORT |= (1<<motorReset)|(1<<motorEnable)|(1<<motorMS0)|(1<<motorMS1); //start with motor disabled, not in reset, 1/16 stepping
  motorPORT &= ~(1<<motorDir)|(1<<motorStep); //dir in reverse, step low, (note ~)

  //CONFIGURE TIMER 1 FOR STEP GENERATION
  TCCR1A = (0<<COM1A1)|(0<<COM1A0)|(0<<COM1B1)|(0<<COM1B0)|(0<<WGM11)|(0<<WGM10);  //CTC on OCR1A
  TCCR1B = (0<<ICNC1)|(0<<ICES1)|(0<<WGM13)|(1<<WGM12)|(0<<CS12)|(0<<CS11)|(1<<CS10);  //CTC on OCR1A, CLK/1
  OCR1A = 921 ;  //921 clock ticks per stepper routine, time unit = 50uS ~= 20KHz
  TIMSK1 = (1<<OCIE1A);  //timer interrupt on
  sei();
}


//USER LOOP
void userLoop(){
};





//--UTILITY FUNCTIONS----
void enableDriver(){
  motorPORT &= ~(_BV(motorEnable));
}

void disableDriver(){
  motorPORT |= _BV(motorEnable);
}

void setForward(){
  motorPORT |= _BV(motorDir);  //pin should be pin# in port
}

void setReverse(){
  motorPORT &= ~(_BV(motorDir));
}
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

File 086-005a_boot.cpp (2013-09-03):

#include <gestalt.h>
#include <avr/io.h>

//CONFIGURE URL
char myurl[] = "http://www.fabunit.com/vn/086-005a_boot.py";

//USER SETUP
void userSetup(){
  setURL(&myurl[0], sizeof(myurl));
  //PIN AND PORT CONFIGURATION FOR SINGLE STEPPER
  IO_ledPORT = &PORTB;
  IO_ledDDR = &DDRB;
  IO_ledPIN = &PINB;
  IO_ledPin = 1<<3;

  IO_buttonPORT = &PORTB;
  IO_buttonDDR = &DDRB;
  IO_buttonPIN = &PINB;
  IO_buttonPin = 1<<2;

  IO_txrxPORT = &PORTD;
  IO_txrxDDR = &DDRD;
  IO_rxPin = 1<<0;
  IO_txPin = 1<<1;

  IO_txEnablePORT = &PORTD;
  IO_txEnableDDR = &DDRD;
  IO_txEnablePin = 1<<2;
}

void userLoop(){
};

//PACKET ROUTER
void userPacketRouter(uint8_t destinationPort){

};

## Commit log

2013-10-15 added cable doc image
2013-10-15 moved some of the board files to their own directory, added the board revision with the mounting holes.
    [086-005.brd, 086-005.sch]
2013-10-18 added the fabnet adapter from mtm.cba.mit.edu/fabinabox/dev/fabnet/overview.html
    [076-000a.brd, 076-000a.sch]
2014-05-02 added new board version with extra connector so you don't have to cable through.
    [086-005.brd, 086-005.sch]
2014-06-22 added an extra connector so you can use multiple cables for connecting
    [086-005.brd, 086-005.sch]
2014-12-03 added BOM for latest board rev (0.3)
    [086-005BOM.csv]
2014-12-12 added a new node for 3d printing heads with connectors for a thermistor, heater wire, and a stepper motor for extrusion of filament. software to follow
    [extrudernode.brd, extrudernode.sch]
2014-12-12 added updated milling files for modela
2014-12-15 added board outline for extruder node
2014-12-15 updated extruder traces with some milling mistake fixes
2015-11-06 added board outline for fabnet adapter
2016-05-04 changed problematic capacitor in the bom to be 50v not 6.3v
    [086-005BOM.csv]
2016-07-07 added a new version for seeed requirement
    [086-005.brd, 086-005.sch, Seeed BOM- Electronics.xlsx]
2016-07-08 oops wrong BOM
    [Rev 0.4 Seeed BOM.xlsx, Seeed BOM- Electronics.xlsx]
2019-03-04 Fix SeeedStudio BOM
    [Rev 0.4 Seeed BOM 2019.xlsx]
